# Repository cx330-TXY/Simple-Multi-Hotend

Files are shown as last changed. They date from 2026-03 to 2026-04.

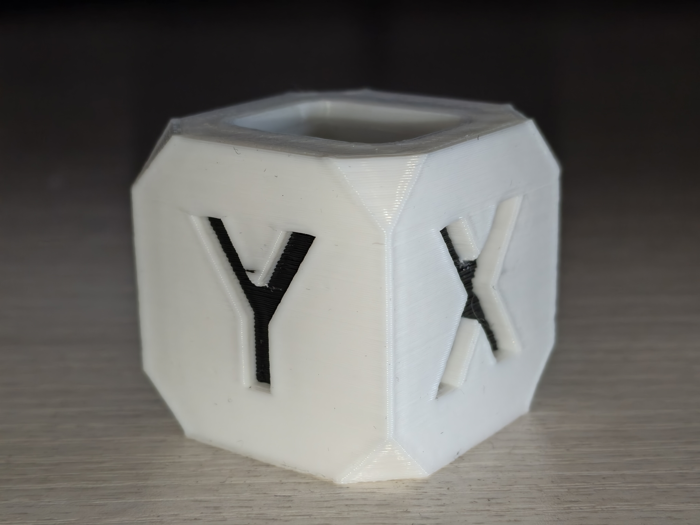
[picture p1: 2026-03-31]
img/IMG_20260307_104415.jpg

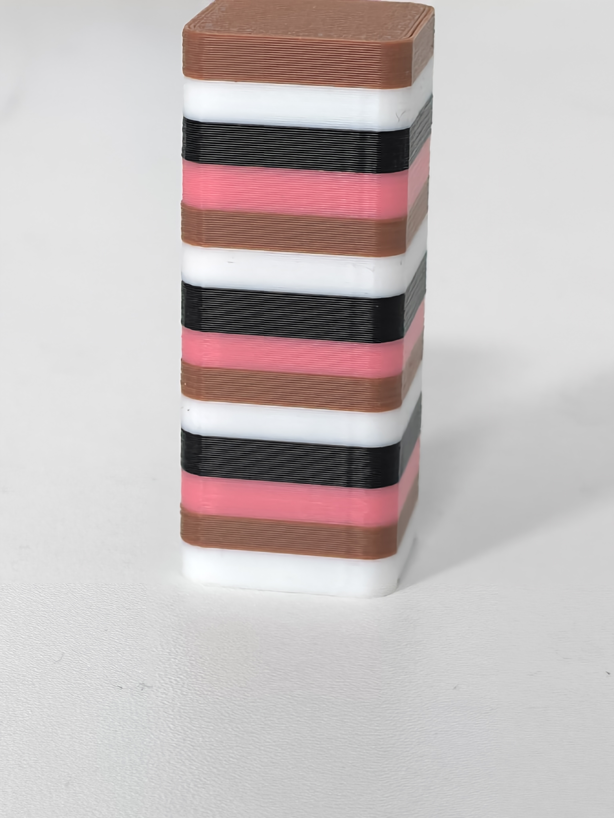
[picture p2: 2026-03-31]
img/IMG_20260326_110722.jpg

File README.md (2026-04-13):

# [Simple-Multi-Hotend]

[Simple-Multi-Hotend]是一种FDM3D打印多材料/多色解决方案。通过在打印打印过程中切换预热好的装载不同耗材的热端实现快速多材料打印。其目标是实现尽可能低成本且简单稳定的多材料打印，为了实现较高的适配性，热端切换只需要打印头XY轴运动就可实现，且切换结构与热端无关，可以通过修改热端固定件等实现其他热端的兼容。
打印头

QQ20260404-193802

---

## 核心特性
- **自动预热**：开启orcaslicer中的Ooze预防功能，会根据自己设定的预热时间提前在切换材料前插入预热命令，切换时释放旧热端并切换到待机温度然后抓取已经预热好的热端，若下一次切换的时间短于加热时间则保持温度不降温。
- **欠驱动切换机构**：采用欠驱动设计不需要额外增加主动元件，利用打印头自身的XY轴运动与停靠坞机械交互来实现热端切换和耗材丝夹紧松开。
- **磁吸麦克斯韦定位耦合机构**：热端模块锁定采用N52磁铁磁吸配合[麦克斯韦耦合](https://en.wikipedia.org/wiki/Kinematic_coupling)定位机构，打印头端有定位销组成的三个槽口，热端模块端有圆头销头部组成的球头。磁吸配合时实现对热端模块空间六自由度的限位，不存在过定位所以即使有加工装配误差以及磨损变形热端模块都能自适应消隙精确定位。
- **自动喷嘴偏移量校准**:采用喷嘴触碰校准器校准每个头XYZ轴相对T0的偏移量，参考[FoxChanger](https://github.com/Noisyfox/FoxChanger/tree/main/NozzleProbe)，需要清理干净喷嘴才能获得正确喷嘴偏移量。不需要每次打印前都校准，通常在刚装配好或者出现撞头等情况需要校准。

## 硬件与软件需求

### 硬件
* **打印机** 原理上支持打印头具有XY移动能力的机型（如voron2.4、voron三叉戟、大鱼TT等）。
* **主板** 由于采用有线加热，每个热端模块具有一个加热片和热敏，可利用主板空余接口来扩展少量热端模块，若需要扩展更多热端模块需要制作[扩展板]( https://oshwhub.com/johnnybyzhang/f103-based-klipper-ext-can-usb)来增加主板的加热棒接口和热敏接口。

### 软件
* **固件** 整体热端切换通过klipper宏命令实现，若需使用喷嘴偏移量校准则需要下载[toolchange](https://github.com/viesturz/klipper-toolchanger)插件，配合自动校准宏来实现。
* **切片软件**：采用Orcaslicer，其他切片软件可自行探索。

## 组成概览

### 组成部分
- 打印头：有除了热端以外的其他部分
- 热端模块：包含热端，接有铁氟龙管和加热片和热敏的线
- 停靠坞：用于存放停靠的热端，可以堵住停靠热端的嘴防止漏料，以及有散热风扇给停靠的热端进行散热（无封箱的采用侧面离心风扇对所有热端进行散热、有封箱的采用每个停靠坞一个轴流风扇）。

### 零件
#### 打印版
- 1.5×5（直径*长）圆柱销：用于构成麦克斯韦耦合定位的槽（×6）
- 3×6（直径*长）圆头销：用于构成麦克斯韦耦合定位的球（一个热端3个）
- 5×20（直径*长）内螺纹圆头销：装配于停靠坞上用于撑开挤出机摆臂（一个停靠坞1个）
- 6×4（直径*厚）N52磁铁：用于吸附热端模块到打印头上和停靠坞上（一个热端3个，一个停靠坞1个，打印头3个）
- M3×25螺丝
- M3×8螺丝
- M3×10螺丝
- M3×12螺丝
- M3×14螺丝
- M3×20螺丝
- M2.5×16螺丝
- M2×8螺丝
- M3×4×4热熔螺母
- HGX挤出机齿轮组
- 4020蜗轮风扇
- 2510轴流风扇
- 欧姆龙微动开关
- 10×2（宽×厚）自粘耐热硅胶条
#### CNC版
CNC件采用嘉立创打样制作（打样零件汇总在CAD文件夹里），目前每个零件都可以免费打样（2026.4.13）
- 1.5×5（直径*长）圆柱销：用于构成麦克斯韦耦合定位的槽（×6）
- 3×6（直径*长）圆头销：用于构成麦克斯韦耦合定位的球（一个热端3个）
- 5×20（直径*长）内螺纹圆头销：装配于停靠坞上用于撑开挤出机摆臂（一个停靠坞1个）
- 6×4（直径*厚）N52磁铁：用于吸附热端模块到打印头上和停靠坞上（一个热端3个，一个停靠坞1个，打印头3个）
- M3×25螺丝
- M3×8螺丝
- M3×10螺丝
- M3×12螺丝
- M3×14螺丝
- M3×20螺丝
- M2.5×16螺丝
- M2×8螺丝
- 内3外5高10隔离柱
- 内3外5高7隔离柱
- 内3外6厚0.5垫片
- 内3外6厚1垫片
- HGX挤出机齿轮组
- 4020蜗轮风扇
- 2510轴流风扇
- 欧姆龙微动开关
- 10×2（宽×厚）自粘耐热硅胶条
- M4*25带孔螺丝
- M2.5外径3长20塞打螺丝（挤出机摆杆转轴）

## 安装与配置指南

### printer.cfg
   Printer.cfg主体可以沿用自己以前的，参考我的printer.cfg里的格式和下面的提示修改，也可以直接用我的然后改成自己主板的引脚。
   1. 引用 toolchange.cfg 和 calibration.cfg。
   2. 仿照extruder1格式定义增加的热端，加热棒热敏引脚按自己主板接线来，挤出机引脚自己编主板上没有的，因为共用E0的挤出机、其他的为虚拟挤出机。
   3. probe采用固定微动，开始打印时热端全部停放于停靠坞中用耐高温硅胶垫堵嘴，加热到目标温度才拿出来解决初始漏料问题，不需要擦嘴，调平时未抓取热端此时微动为打印头最低点。还未支持其他调平方式，建议直接参考我的probe相关配置包括网床和调平的配置（主要是增加了调平前释放抓取的热端）。
   4. 添加停靠坞散热风扇配置，停靠坞散热风扇和喉管冷却风扇关联的挤出机里添加所有挤出机。
   5. 修改打印开始gcode，实现打印前自动给要使用的热端进行挤出划线。
   6. 修改打印结束gcode，添加UNTOOL命令保证打印完自动卸载热端，让下次打印时不用自己手动取下热端。增加关闭所有热端加热命令。
### toolchange.cfg
   1. 添加toolchange.cfg。添加成功后仪表盘界面会出现T0、T1、T2以及、UNTOOL命令，（没调坐标先别点、会直接撞）点击T0是抓去T0，抓取T0后再点击T1坐标会自动卸载T0然后抓取T1，点击UNTOOL是卸载当前热端。
   2. 固定停靠坞以及调整停靠坞坐标：手动把热端装到打印头上，把打印头拖动到X轴最右边，再往前拖动，然后把第一个停靠坞固定在能刚好让热端锁定螺丝穿过停靠坞大孔的位置（这个位置即为第一个停靠坞的坐标），然后取下热端，点击全部归位，再把热端装到打印头上，慢慢移动打印头到刚才找到的停靠坞位置让锁定螺丝穿过停靠坞大孔，记下此时的坐标将其填入toolchange里T0的停靠坞位置，一个停靠坞占30mm宽度，其他停靠坞坐标用等差数列得到，如有误差可自己微调每一个停靠坞的坐标。 
   
   
   3. 正确设置坐标后，注释正常速度，解除测试速度注释，用慢速进行切换测试，（方便看到没对齐直接点急停）。
   4. 测试速度切换正常后，注释测试速度，解除正常速度注释（可以根据自己机器情况自己测试出更为合适的速度）。
### calibration.cfg
   1. 下载[toolchange](https://github.com/viesturz/klipper-toolchanger)插件
   1. 添加calibration.cfg
   2. 归位xyz，调平完成后，固定好校准器，点击T0抓去第一个热端，移动至喷嘴尖端刚好位于校准器中心正上方距离1mm左右，记下这个时候的坐标，填入calibration.cfg里校准器坐标处，然后还需要在里面自己定义一个停靠坞范围外的安全位置，防止校准的时候撞到停靠坞里的其他热端。
   3. 坐标设置好后输入 CALIBRATE_TOOL TOOL=_ 可以校准指定热端（需要先校准T0），输入 CALIBRATE_ALL_TOOLS 可以校准全部（需要设定好有哪些热端）。
### orcaslicer
   1. 修改打印机gcode里起始和耗材丝更换gcode、设置更多挤出机、设置挤出机回抽。
   
   
   

   2. 工艺栏里开启擦拭塔（如果料和参数调得好，且模型不涉及快速微小挤出，可以把模型拖到停靠坞旁边关掉擦料塔尝试无擦料塔打印）和自动预热（Ooze）。
   

## 注意事项
- 打印件采用abs打印，4层墙，60%填充。
- 挤出机弹簧不能拧太紧，过紧会导致摆臂转动的时候发生形变导致挤出轮张不开，具体情况视自己打印出摆臂的实际刚性而定。
- 为了减少热量传导效率，用到的TZ2.0热端需要去掉固定加热块的两个螺丝，仅靠侧面顶丝固定。

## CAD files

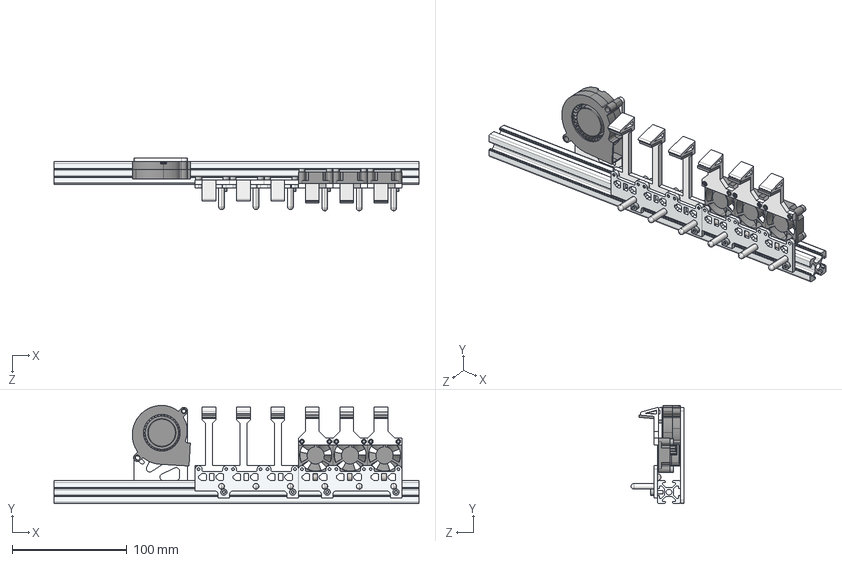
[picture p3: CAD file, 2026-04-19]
CAD/停靠坞.STEP
318.0 x 85.5 x 46.0 mm
热端停靠坞多联CNC x 2
Fan 3010 x 3
不锈钢内螺纹圆弧销 x 6
LE-6-2020铝型材[LE-6-2020-B-OO-240]_LE-6-2020-B-OO-240
堵嘴固定件（封箱版） x 3
耐热硅胶垫 x 6
圆柱头螺栓_M3*8 x 4
圆柱头螺栓_M3*12 x 12
热熔螺母M3 4 4 x 6
N52磁铁 6 4 x 3
垫圈_3.2*6*1 x 6
5015离心风扇
5015固定
堵嘴固定件（无封箱版） x 3
圆柱头螺栓_M3*6 x 6
沉头螺栓_M3*6 x 6

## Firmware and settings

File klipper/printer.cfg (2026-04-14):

#####################################################################
#                               文件调用                               #
#####################################################################
[include fluidd.cfg]          # FLUIDD调用文件。
#[include mainsail.cfg]        # MAINSDIL调用文件。
[include toolchange.cfg]
[include calibration.cfg]
#[include plr.cfg]
#####################################################################
#                               主板配置                               #
#####################################################################
[mcu]
serial: /dev/serial/by-id/usb-Klipper_stm32h723xx_12345-if00
[mcu host]
serial: /tmp/klipper_host_mcu

#####################################################################
#                            副板扩展配置                             #
#####################################################################
[mcu expander]
# 这里填入你在第一步获取到的新主板ID
serial: /dev/serial/by-id/usb-Klipper_stm32f072xb_3F0035000357465036383420-if00 
#####################################################################
#                            机型和加速度                            #
#####################################################################
[printer]                       # 打印机设置
kinematics: corexy              # 运动学结构分为：笛卡尔和corexy等等。笛卡尔：cartesian
max_velocity: 600               # 打印机最大速度   
max_accel: 30000                 # 最大加速度 
max_z_velocity: 30              # z轴最大速度
max_z_accel: 300                # z轴最大加速度
square_corner_velocity: 5.0     # 方形拐角速度，小一点可以有效避免平台重带来的惯性
#####################################################################
#                             温度监控                               #
#####################################################################
[temperature_sensor FLY-Pi]
sensor_type: temperature_host

#[temperature_sensor Fly-C8p]     # FLY主板温度（可自行重命名）
#sensor_type: temperature_mcu     # 关联mcu（默认）

# [temperature_sensor Box]          # 箱内温度温度 （需要增加一颗温感,参考配置）
# sensor_type: ATC Semitec 104GT-2  # 传感器型号
# sensor_pin: PA4                   # 信号接口

#####################################################################
#             X/Y步进电机设置 (X/Y Stepper Settings)                 # 
#####################################################################
#   B Motor ---- Motor A 
#   |                  |
#   |------挤出机-------|
#   |                  |
#   |                  |
#          正前方   
#####################################################################
#                  X 轴步进电机 (B Motor)                            #
#####################################################################
[stepper_x]
step_pin: PE5                       # X轴电机脉冲引脚设置
dir_pin: !PA8                        # X轴电机运行引脚设置,方向按实际判断，加感叹号会让运行方向反转
enable_pin: !PA15                   # X轴电机使能引脚设置,使能引脚需要加感叹号，否者电机不工作
rotation_distance: 40               # 主动带轮周长mm（2GT-20T带轮40，2GT-16T带轮32）
microsteps: 64                      # 电机细分设置，细分越高，质量越高，但主控负荷越大
full_steps_per_rotation: 200        # 电机单圈所需脉冲数（1.8度电机:200，0.9度电机:400）
endstop_pin:tmc2209_stepper_x:virtual_endstop                   # 限位开关PIN脚,建议常闭然后添加！反转状态,位置在io-3 !PB3 
###接常闭后是触发状态，加感叹号可以反转这个状态，万一断线时候可以避免撞机
position_min: -10                     # X轴的最小行程
position_endstop: 245            # 限位开关的位置 (250mm-300mm-350mm)
position_max: 245                   # X轴的最大行程 (250mm-300mm-350mm)
homing_speed: 50                    # 复位速度，最大为100.归位速度建议别太快
homing_retract_dist: 0              # 第一次触发复位开关之后的后退距离
#--------------------------------------------------------------------
[tmc2209 stepper_x]                 # X 驱动配置 -TMC2209
uart_pin: PC9                       # 通讯端口Pin脚定义
interpolate: False                  # 否开启256微步插值，建议关闭（开启是True，关闭是False）
run_current: 1.2                   # 电机运行电流值（单位：mA）
sense_resistor: 0.110               # 驱动采样电阻不要改
driver_SGTHRS:90
diag_pin:^PD9
#stealthchop_threshold: 100          # 静音阀值（如果不需要静音，请将数值改为0）
#####################################################################
#                  Y 轴步进电机 (A Motor)                            #
#####################################################################
[stepper_y]
step_pin: PE4                       # Y轴电机脉冲引脚设置
#step_pin: PE8
dir_pin: PC11                      # Y轴电机运行引脚设置,方向按实际判断，加感叹号会让运行方向反转
#dir_pin: PA7
enable_pin: !PC12                   # Y轴电机使能引脚设置,使能引脚需要加感叹号，否者电机不工作
#enable_pin: PA6
rotation_distance: 40               # 主动带轮周长mm（2GT-20T带轮40，2GT-16T带轮32）
microsteps: 64                      # 电机细分设置，细分越高，质量越高，但主控负荷越大
full_steps_per_rotation: 200        # 电机单圈所需脉冲数（1.8度电机:200，0.9度电机:400）
#ndstop_pin:tmc2209_stepper_y:virtual_endstop                   # 限位开关PIN脚,建议常闭然后添加！反转状态,位置在io-0 !PD2
endstop_pin:^!PD10
###接常闭后是触发状态，加感叹号可以反转这个状态，万一断线时候可以避免撞机
position_min: -33                     # Y轴的最小行程
position_endstop: 229               # 限位开关的位置 (250mm-300mm-350mm)
position_max: 229                   # Y轴的最大行程 (250mm-300mm-350mm)
homing_speed: 50                    # 复位速度，最大为100        归位速度建议别太快
homing_retract_dist: 5              # 第一次触发复位开关之后的后退距离 5
#step_pulse_duration: 0.000004
#--------------------------------------------------------------------
[tmc2209 stepper_y]                 # Y驱动配置 -TMC2209
uart_pin: PC10                      # 通讯端口Pin脚定义
interpolate: false                  # 否开启256微步插值，建议关闭（开启是True，关闭是False）
run_current: 1.2                    # 电机运行电流值（单位：mA）
sense_resistor: 0.110               # 驱动采样电阻不要改
driver_SGTHRS:87
diag_pin:^PD8
#stealthchop_threshold: 100          # 静音阀值（如果不需要静音，请将数值改为0）
#####################################################################
#                     Z轴步进电机 （Z Stepper Settings）              #
#####################################################################
#   |----- Z1 -----|
#   |              |
#   |              |
#   |              |
#   Z0----显示屏----Z2

#####################################################################
#                           Z轴步进电机                              #
#####################################################################
##    Z步进电机 - 左前方
[stepper_z]
step_pin: PE3                 # z轴电机脉冲引脚设置
dir_pin:  !PD1                 # z轴电机方向引脚设置,方向引脚需要按实际判断，加感叹号会让运行方向反转
enable_pin: !PD2               # z轴电机使能引脚设置,使能引脚需要加感叹号，否者电机不工作
### T8x4丝杠。旋转一圈，热床床可移动4毫米 
## 请根据购买的丝杆参数进行修改
rotation_distance: 8          # 丝杆导程为 8，请根据你的实际使用情况修改，总共需要修改3处
full_steps_per_rotation: 200  # 电机单圈所需脉冲数（1.8度电机:200，0.9度电机:400)
microsteps: 16                # 电机细分设置,细分越高，质量越高，但主控负荷越大
endstop_pin: probe:z_virtual_endstop            # 限位开关PIN脚,建议常闭然后添加！反转状态,位置在io-1
## position_endstop 是喷嘴相对于打印表面(Z0)到Z限位停止触发点的位置(单位:mm)
## 正数值 = 高于平台的终止点，负数值 = 低于平台的的终止点
## 增加position_ endstop的数值会使喷嘴更靠近床
## 在运行Z_ENDSTOP_CALIBRATE之后，position_endstop将存储在CFG配置的最后
position_min: -15             # Z轴的最小行程（配置喷嘴清洁需要-5左右）
position_max: 180             # Z轴的最大行程 (250mm-300mm-350mm)
homing_speed: 10               # 复位速度-最大 20
second_homing_speed: 3        # 二次复位速度-最大 10
homing_retract_dist: 0        # 后撤距离
step_pulse_duration: 0.000004 # step信号保持时间（4us）

[tmc2209 stepper_z]
uart_pin: PD0                 # 驱动通信端口
interpolate: false            # 微步插值256
run_current: 0.8              # 运行电流mA
sense_resistor: 0.110         # 驱动采样电阻不要改
stealthchop_threshold: 500    # 静音阀值（如果不需要静音，请将数值改为0）
#--------------------------------------------------------------------
##    Z1 步进电机 - 后方
[stepper_z1]
step_pin: PE2                # z1轴电机脉冲引脚设置
dir_pin:  !PD4               # z1轴电机方向引脚设置,方向引脚需要按实际判断，加感叹号会让运行方向反转
enable_pin: !PD5              # z1轴电机使能引脚设置,使能引脚需要加感叹号，否者电机不工作
### T8x4丝杠。旋转一圈，热床床可移动4毫米 
## 请根据购买的丝杆参数进行修改
rotation_distance: 8          # 丝杆导程为 8
full_steps_per_rotation: 200  # 电机单圈所需脉冲数（1.8度电机:200，0.9度电机:400
microsteps: 16                # 电机细分设置,细分越高，质量越高，但主控负荷越大
step_pulse_duration: 0.000004 # step信号保持时间（4us）
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

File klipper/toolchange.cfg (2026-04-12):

#=================================================
# 1. 参数集中管理
#=================================================
[gcode_macro _toolchanger_cfg]
description: 工具切换参数配置

# --- 换刀抬升与速度 ---
variable_z_hop:       0.4   #换头抬升高度
variable_feed_z:      600   #抬升速度
variable_feed_fast:   24000 #工作速度（空驶）
#variable_feed_fast:   2000 #测试速度
variable_feed_slow:   5000  #工作速度（受力）

# --- 换刀回抽/清洗配置 ---
variable_swap_retract_len: 0   # [A] 释放回抽：放回底座时抽多少
variable_swap_prime_len:   0   # [B] 抓取清洗：抓取时挤出多少
variable_swap_retract_spd: 1000

# ========================================================
# 【停靠坞运动逻辑参数】
# ========================================================
variable_dock_shift_x: -4.0   # 横移开挤出机距离
variable_dock_dodge_y: 14     # 避让动作的 Y 轴相对位移
variable_dock_safe_y:  28     # 安全拔出的 Y 轴相对位移

#---------------------------------------------------------
# 各热端参数配置
#---------------------------------------------------------
# T0 配置
variable_t0_dock_x: 245.0     # T0 热端进入停靠坞大孔X坐标
variable_t0_dock_y: -25       # T0 热端进入停靠坞大孔Y坐标
variable_t0_offset_x: 0.0
variable_t0_offset_y: 0.0
variable_t0_offset_z: 0.0

# T1 配置
variable_t1_dock_x: 215.0    
variable_t1_dock_y: -25
variable_t1_offset_x: -0.190625  #相对T0喷嘴位置偏移量（执行喷嘴偏移量校准后手动填入）
variable_t1_offset_y: 0.232812
variable_t1_offset_z: 0.0975

# T2 配置
variable_t2_dock_x: 185.0
variable_t2_dock_y: -25
variable_t2_offset_x: 0.26875
variable_t2_offset_y: 0.24375
variable_t2_offset_z: 0.1225

# T3 配置
variable_t3_dock_x: 155.0
variable_t3_dock_y: -25
variable_t3_offset_x: 0.768750
variable_t3_offset_y: 0.31875
variable_t3_offset_z: 0
gcode:

#=================================================
# 2. 切换热端命令（根据自己的热端数添加对应数量）
#=================================================

[gcode_macro T0]     #输入T0，当前有热端则卸载当前热端抓取T0，无热端则直接抓取T0
gcode: change_tool T=0

[gcode_macro T1]
gcode: change_tool T=1

[gcode_macro T2]
gcode: change_tool T=2

[gcode_macro T3]
gcode: change_tool T=3

[gcode_macro UNTOOL]  #卸载当前热端
gcode: change_tool T=-1

#=================================================
# 3. 状态变量（记录当前抓取头）
#=================================================
[gcode_macro _tool_status]
variable_current_tool: -1
gcode:

#=================================================
# 4. 释放热端
#=================================================
[gcode_macro _release_tool]
gcode:
    {% set cfg = printer["gcode_macro _toolchanger_cfg"] %}
    {% set tool = params.TOOL|int %}
    {% set prefix = "t" ~ tool %}
    {% set active_extruder = printer.toolhead.extruder %}
    
    # 获取当前喷头的核心点坐标和相对位移
    {% set dock_x = cfg[prefix + "_dock_x"] %}
    {% set dock_y = cfg[prefix + "_dock_y"] %}
    {% set shift_x = cfg.dock_shift_x %}
    {% set dodge_y = cfg.dock_dodge_y %}
    {% set safe_y  = cfg.dock_safe_y %}

    {% set msg = "正在放回 T%d" % tool %}   M118 {msg}

    # --- [A] 释放回抽 (防止底座溢料) ---
    {% set cur_temp = printer[active_extruder].temperature|float %}
    {% set min_temp = printer.configfile.settings[active_extruder].min_extrude_temp|default(170)|float %}
    {% if cur_temp >= min_temp %}
       M83  
       G1 E-{cfg.swap_retract_len} F{cfg.swap_retract_spd} 
       M400 
    {% else %}
       M118 温度不足({cur_temp})，跳过释放回抽。
    {% endif %}

    # --- 开始释放动作 (抓取动作的逆序) ---
    G90 
    # 1. 带热端走到到X轴对准停靠坞大孔，Y轴位于停靠坞外（停靠坞入口）
    G0 X{dock_x} Y{dock_y + safe_y} F{cfg.feed_fast}
    
    # 2. 带热端Y轴移动完全进入停靠坞
    G0 X{dock_x} Y{dock_y} F{cfg.feed_fast}
    M400
    
    # 3. 横移打开挤出机摆臂
    G0 X{dock_x + shift_x} Y{dock_y} F{cfg.feed_slow}
    
    # 4. 打印头离开停靠坞拔开与打印头磁吸锁定的热端
    G0 X{dock_x + shift_x} Y{dock_y + dodge_y} F{cfg.feed_slow}
    
    # 5. 反向横移闭合挤出机摆臂
    G0 X{dock_x} Y{dock_y + dodge_y} F{cfg.feed_slow}
    
    # 6. 完全离开停靠坞（停靠坞入口）
    G0 X{dock_x} Y{dock_y + safe_y} F{cfg.feed_fast}
    M400

#=================================================
# 5. 抓取热端
#=================================================
[gcode_macro _pickup_tool]
gcode:
    {% set cfg = printer["gcode_macro _toolchanger_cfg"] %}
    {% set tool = params.TOOL|int %}
    {% set prefix = "t" ~ tool %}
    {% set current_heater = "extruder" if tool == 0 else ("extruder" ~ tool) %}
    
    # 获取当前喷头的核心点坐标和相对位移
    {% set dock_x = cfg[prefix + "_dock_x"] %}
    {% set dock_y = cfg[prefix + "_dock_y"] %}
    {% set shift_x = cfg.dock_shift_x %}
    {% set dodge_y = cfg.dock_dodge_y %}
    {% set safe_y  = cfg.dock_safe_y %}

    {% set msg = "【抓取】正在抓取 T%d" % tool %}   M118 {msg}
    
    # --- 开始抓取动作 ---
    G90
    # 1. 到达停靠坞入口
    G0 X{dock_x} Y{dock_y + safe_y} F{cfg.feed_fast}
    
    # 2. Y轴前进到避让位置（让摆臂能摸到摆臂撑杆，同时打印头不撞到停靠的热端）
    G0 X{dock_x} Y{dock_y + dodge_y} F{cfg.feed_fast}
    
    # 3. 横移开挤出机
    G0 X{dock_x + shift_x} Y{dock_y + dodge_y} F{cfg.feed_slow}
    
    # 4. Y轴移动完全进入停靠坞（打印头与热端磁吸结合）
    G0 X{dock_x + shift_x} Y{dock_y} F{cfg.feed_slow}
    M400
    
    # 5. 反向横移闭合挤出机夹紧耗材丝
    G0 X{dock_x} Y{dock_y} F{cfg.feed_slow}
    
    # <<< 停靠坞内挤出补偿 >>>
    {% set cur_temp = printer[current_heater].temperature|float %}
    {% set min_temp = printer.configfile.settings[current_heater].min_extrude_temp|default(170)|float %}
    {% if cur_temp >= min_temp %}
         M83 
         G1 E{cfg.swap_prime_len} F{cfg.swap_retract_spd} 
         M400
    {% else %}
         M118 温度不足({cur_temp})，跳过抓取处理。
    {% endif %}

    # 6. 完全离开停靠坞（停靠坞入口）
    G0 X{dock_x} Y{dock_y + safe_y} F{cfg.feed_fast}
    M400
     
#=================================================
# 6. 主切换宏
#=================================================
[gcode_macro change_tool]
gcode:
    {% set new_tool = params.T|default(-1)|int %}
    {% set old_tool = printer["gcode_macro _tool_status"].current_tool|int %}
    {% set cfg = printer["gcode_macro _toolchanger_cfg"] %}

    {% if new_tool == old_tool %}
        M118 目标状态与当前一致(T{new_tool})，无需操作。
    {% else %}
        {% if new_tool == -1 %}
            M118 收到卸载指令：正在卸载 T{old_tool} ...
        {% else %}
            M118 切换工具: T{old_tool} -> T{new_tool}
        {% endif %}

        #保存换头前状态
        SAVE_GCODE_STATE NAME=tool_change

        #换头前屏蔽断料检测
        SET_FILAMENT_SENSOR SENSOR=tool_sensor ENABLE=0
        
        #抬升
        G91
        G0 Z{cfg.z_hop} F{cfg.feed_z}
        G90
        
        #清除偏移偏移量采用统一的停靠坞坐标
        SET_GCODE_OFFSET X=0 Y=0 Z=0

        #释放旧工具
        {% if old_tool != -1 %}
            _release_tool TOOL={old_tool}
        {% else %}
            M118 当前无工具，跳过释放。
        {% endif %}

        #抓取新工具
        {% if new_tool != -1 %}
            {% set next_heater = "extruder" if new_tool == 0 else ("extruder" ~ new_tool) %}
            {% set target_temp = printer[next_heater].target|float %}
            {% if target_temp > 0 %}
                {% if printer[next_heater].temperature < (target_temp - 2) %}
                    M118 T{new_tool} 预热中...
                    TEMPERATURE_WAIT SENSOR={next_heater} MINIMUM={target_temp}
                {% endif %}
            {% endif %}

            ACTIVATE_EXTRUDER EXTRUDER={next_heater}
            SYNC_EXTRUDER_MOTION EXTRUDER=extruder MOTION_QUEUE={next_heater}

            _pickup_tool  TOOL={new_tool}
        {% else %}
            M118 工具已卸载。
        {% endif %}

        #更新状态变量
        SET_GCODE_VARIABLE MACRO=_tool_status VARIABLE=current_tool VALUE={new_tool}

        #恢复到换头前位置
        RESTORE_GCODE_STATE NAME=tool_change MOVE=0 
        
        #应用喷嘴偏移量
        {% if new_tool != -1 %}
            {% set prefix = "t" ~ new_tool %}
            {% set off_x = cfg[prefix + "_offset_x"]|default(0.0)|float %}
            {% set off_y = cfg[prefix + "_offset_y"]|default(0.0)|float %}
            {% set off_z = cfg[prefix + "_offset_z"]|default(0.0)|float %}
            SET_GCODE_OFFSET X={off_x} Y={off_y} Z={off_z} MOVE=0
        {% endif %}

        #换头后断料检测
        {% if new_tool != -1 %}
            M400     ; 强制等待机器走完所有的抓取和恢复物理坐标动作
            G4 P200  ; 停顿 0.2 秒
            _VERIFY_TOOL_AND_ENABLE_SENSOR ; 调用独立子宏进行判定
        {% endif %}
        # 如果 new_tool 是 -1 (UNTOOL卸载)，就不进行检测，保持传感器关闭即可。

    {% endif %}

#断料与换头失败检测开关定义
[filament_switch_sensor tool_sensor]
switch_pin: ^PA0 
pause_on_runout: False
runout_gcode:
    { action_respond_info("错误：打印中断料报警！已暂停打印。") }
    PAUSE # 打印过程中触发（断料）时的动作
insert_gcode:
    { action_respond_info("耗材已插入。") } # 插入耗材时的动作

#断料与换头失败检测
[gcode_macro _VERIFY_TOOL_AND_ENABLE_SENSOR]
description: 在抓取完成后，读取微动开关状态以判断是否抓取失败
gcode:
    {% set has_filament = printer["filament_switch_sensor tool_sensor"].filament_detected %}
    
    {% if has_filament %}  # 开关处于正常状态
        { action_respond_info("换头成功，耗材状态正常，重新开启断料检测。") }
        SET_FILAMENT_SENSOR SENSOR=tool_sensor ENABLE=1  # 恢复断料检测监控
    {% else %}  # 开关处于异常触发状态
        { action_respond_info("致命错误：换头失败（未抓到喷头）或新喷头无耗材！已紧急暂停！") }
        PAUSE
    {% endif %}
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

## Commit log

2026-04-07 Update CNC components list in README
    Added additional screws and components to the CNC section of the README.
2026-04-12 Refactor tool change configuration and macros
    [toolchange.cfg]
2026-04-12 Update print statement from 'Hello' to 'Goodbye'
    [printer.cfg]
